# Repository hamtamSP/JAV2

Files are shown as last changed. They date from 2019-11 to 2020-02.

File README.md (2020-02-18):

# JAV²




## JAV² Tree Planting Vehicle

The JAV² Tree Planting Vehicle is inspired by the [#teamtrees](https://teamtrees.org/) initiative to plant 20 million trees before 2020. Hence, we created a Tracked Vehicle that can travel through uneven terrain to plant seeds so that they can turn into trees. The JAV² Tree Planting Vehicle is designed to be controlled through Wifi with a mobile device to enable it to plant the seeds in remote areas.

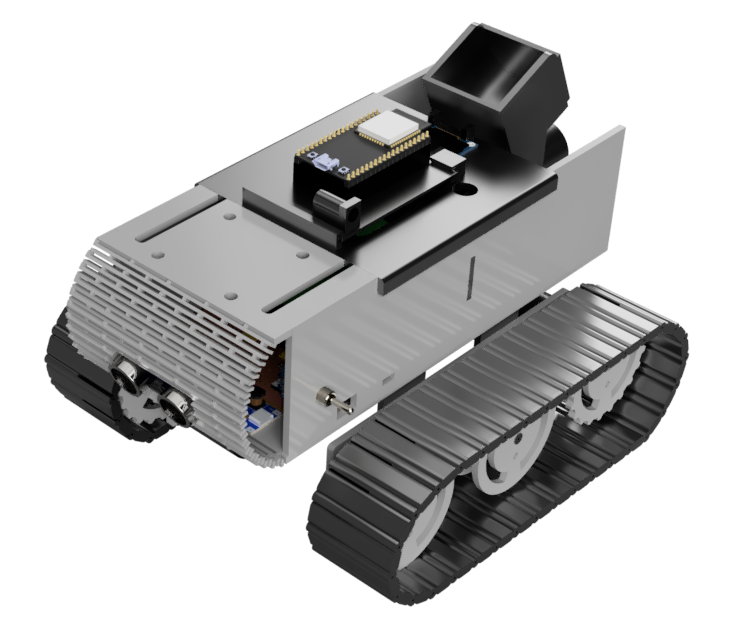
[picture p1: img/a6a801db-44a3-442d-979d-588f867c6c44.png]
JAV² Tree Planting Vehicle


## Table of Contents

- [Documentation](#documentation)
- [Features](#features)
- [Setup](#setup)
- [What You Will Need](#what-you-will-need)
- [Contributors](#contributors)

## Documentation

Documentations for JAV² can be found on GitHub at [https://github.com/hamtamSP/JAV2/blob/master/docs/Documentation.md](https://github.com/hamtamSP/JAV2/blob/master/docs/Documentation.md).

## Features

- Wireless Connectivity with Wifi.
- Auto Seed Dispensing
- Travel on Uneven Terrain

## What You Will Need

- JAV² Tree Planting Vehicle
- Seeds

## Setup

Fill Up the Hopper with Seeds.

Turn on the Tree Planting Vehicle by using the power switch located on the right side of the robot.

Connect to the Wireless AP on the ESP32 using the details on the OLED Screen.

Follow the instructions on the OLED Screen and Enter your wireless network credentials.

Connect to your wireless network and use the details on the OLED Screen to control the Tree Planting Vehicle.

## Contributors

Contributors to JAV² are listed here in alphabetical order. More detailed information about contributions can be found using the [git-commit history](https://github.com/hamtamSP/JAV2/commits/master) of the main branch.

- [@Darkmidget](https://github.com/Darkmidget) (Vincent Ho)
- [@DsouzaVirgil](https://github.com/DsouzaVirgil) (Virgil)
- [@hamtamSP](https://github.com/hamtamSP) (Arian Yap)
- [@JerenTong](https://github.com/JerenTong) (Jeren Tong)

### Blogs

Blogs can be found at:
- [Vincent](https://github.com/hamtamSP/JAV2/tree/master/Vincent_Adventure)
- [Virgil](https://github.com/hamtamSP/JAV2/tree/master/Virgil)
- [Arian](https://github.com/hamtamSP/JAV2/tree/master/Arian)
- [Jeren](https://github.com/hamtamSP/JAV2/tree/master/Jeren)

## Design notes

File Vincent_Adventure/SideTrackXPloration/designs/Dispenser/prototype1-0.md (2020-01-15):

# Dispenser 1.0 (G2 - Pen Design)

## Introduction
When I was in primary school, I like to make things that wasn't meant for the purpose of the product. One of them is a G2-Pen gun, where I disassemble the used pen and reconfigure it into a projectile shooter.

For this case, I will need to reconfigure the barrel size for the sapling to fit in the loading system. I will also redesign the firing system so that the firing force will be the sapling roots and not the leaves or stem. In order to ensure that the saplings is planted firmly to the ground, the saplings will have a tiny rock(Weight) in the roots system so that dispenser will have enough force to punch the saplings into the ground.

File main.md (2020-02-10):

# JAV²
[About Us]()

This site will be used as a group documentation when the project starts officially

This is the link to our contributions and research:

* [Hours Clocked](https://docs.google.com/spreadsheets/d/1DFZNll1I7CO4VDM-ied0fAtll_ErM5nZQO0H-ZwF12Y/edit#gid=0)

* [Group research and findings]()

* [Schematic](https://github.com/hamtamSP/JAV2/blob/master/Schematic-1.svg)

This will be our Individual Blogs
* [Vincent_Adventure](https://github.com/hamtamSP/JAV2/tree/master/Vincent_Adventure/Weekly)
*
## Problem Statements
* Tree  

## Idea Generation

* Tree planter

## What we want our Vehicle to do?
* What is the maximum velocity of the vehicle?
* How many horsepower does the vehicle need?
* How many horsepower does the vehicle need?
* What will be the energy consumption of the vehicle?
* How long does it take for the vehicle to come to stop?
* What happens if shock-absorbers don’t work?
* How to re-gain lost adhesion of the tire?
* What happens when the brake is suddenly applied during cornering?
* Understanding active vehicle safety

## Vehicle Drawing
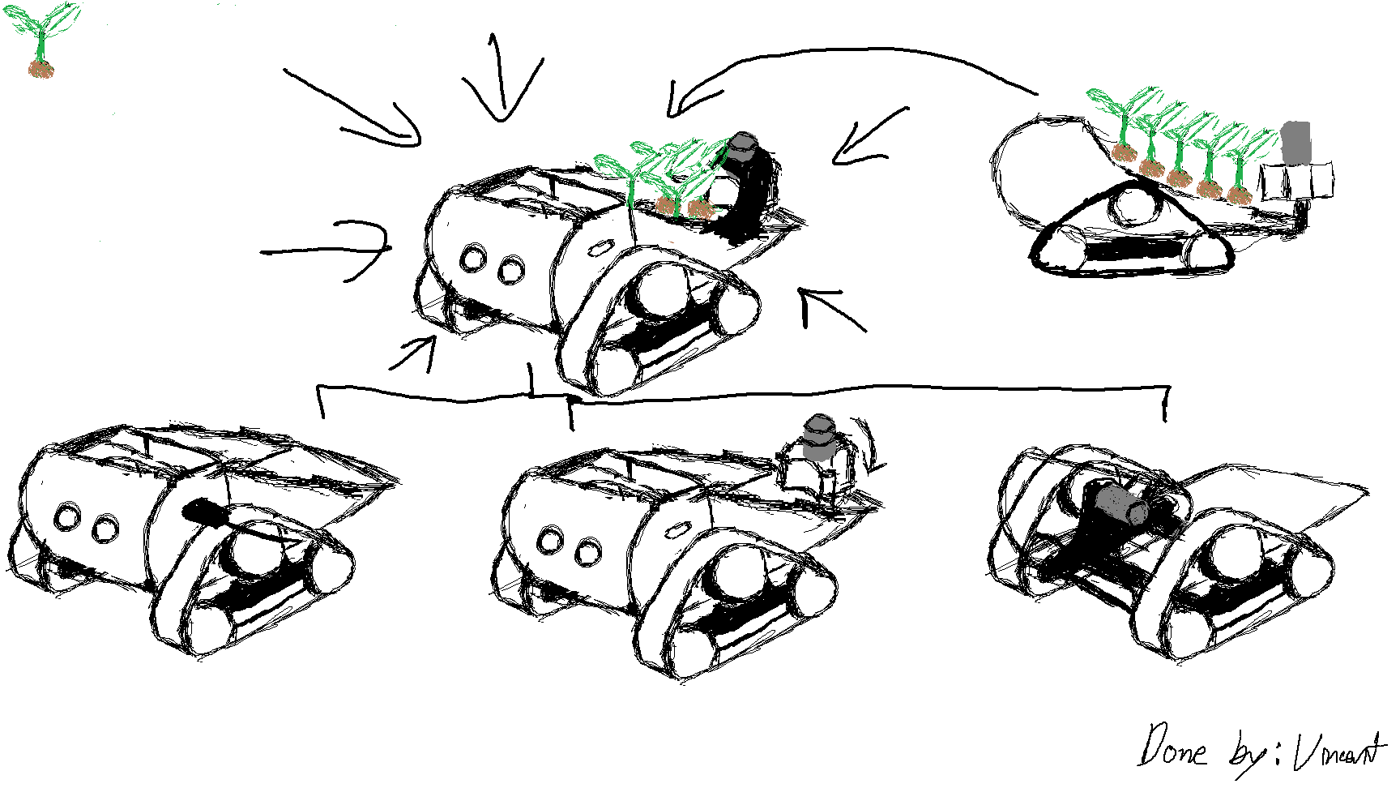
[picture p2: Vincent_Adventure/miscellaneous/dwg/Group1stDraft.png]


## Source Codes
* [Vehicle Run](https://github.com/hamtamSP/JAV2/blob/master/Vincent_Adventure/Blog/Source_code/vehicle%20run%20test%20(forward).py)
* [Vehicle Run with Web Server](https://github.com/hamtamSP/JAV2/blob/master/Vincent_Adventure/Blog/Source_code/WebControlEsp32.py)
* [OLED Library Code](https://github.com/hamtamSP/JAV2/blob/master/Virgil/ssd1306.py)
* [OLED Test Code](https://github.com/hamtamSP/JAV2/blob/master/Virgil/main.py)

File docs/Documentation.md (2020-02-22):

---
title: Documentation
subtitle: Documentation Page for JAV²
layout: page
show_sidebar: false
menubar: documentation
hide_footer: true
---


## Table of Contents

- [Getting Started](#getting-started)
- [Electrical Components](#electrical-components)
  - [Charging Circuit](#charging-circuit)
  - [Boost Ciruit](#boost-circuit)
  - [Battery Monitor](#battery-monitor)
- [Software](#software)
  - [Installation of Software](#installation-of-software)
  - [ESP32 Setup](esp32-setup)

## Getting Started

Below are the Components That are Used

- ESP32
- HC-SR04 Ultrasonic Sensor
- L298N H-Bridge
- 2 x TP4056 Charging Module
- 2 x 18650 Battery
- 2 x 1n4001 Diode
- DPDT Switch
- 2 x Boost Converter
- SG90 Servo
- 2 x Motors
- I2C OLED Display
- 2 x 3.9MΩ Resistors
- 2 x 2.2MΩ Resistors

To Program the ESP32, You will also need the following Software
- [Python](https://www.python.org/downloads/)
- [ESPTool](https://github.com/espressif/esptool)
- [Thonny](https://thonny.org/)
- [MicroPython](https://micropython.org/download)

## Electrical Components

### Charging Circuit

The TP4056 Charging Module is a Single Cell Charging Board. Hence, in order to charge two batteries at the same time, we will connect the 2 TP4056 Modules in Parallel. This allows us to take advantage of the protection features of the board as well as the capacity of the 2 batteries. The outputs of each TP4056 Module is then connected to a 1n4001 Diode to prevent reverse current due to differences in voltages from the 2 modules. The 2 Diodes are then connect to a DPDT Switch actings as a ON/OFF Switch for the Tree Planting Vehicle and the 2 connections are conbimed later. This can be shown in the schematics provided below.

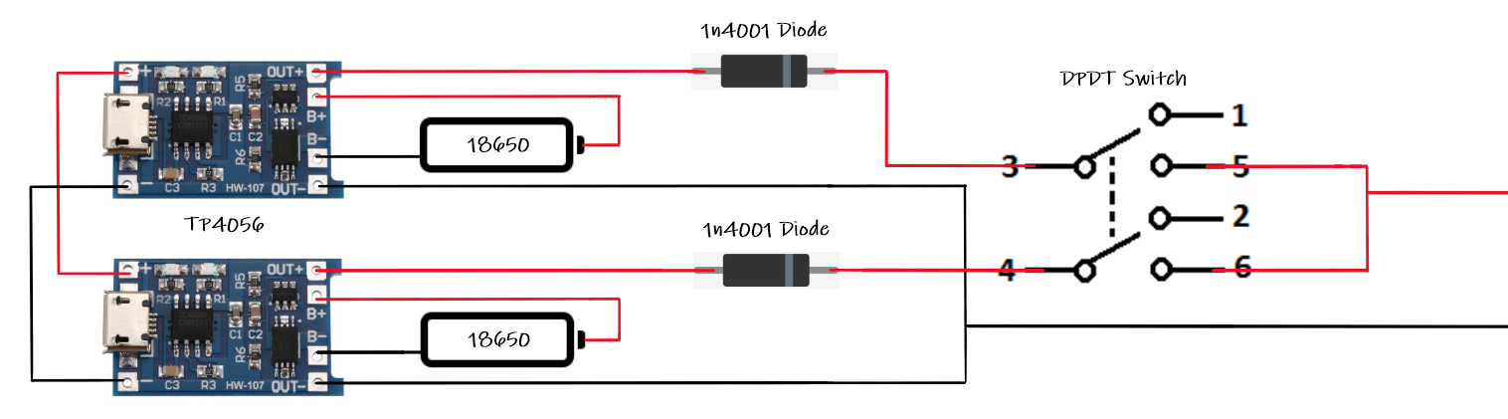
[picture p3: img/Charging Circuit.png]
Charging Circuit


### Boost Circuit

By connecting the output from the charging circuit to the input of the Boost Converter, we Can boost the voltage coming from the TP4056 to 11V for the L298N H-Bridge which is connected to the Output of the Boost Converter. The 5V Rail of the L298N can then be used to supply power to the ESP32 and the other pheripherials. This can be shown in the Schematics provided below.

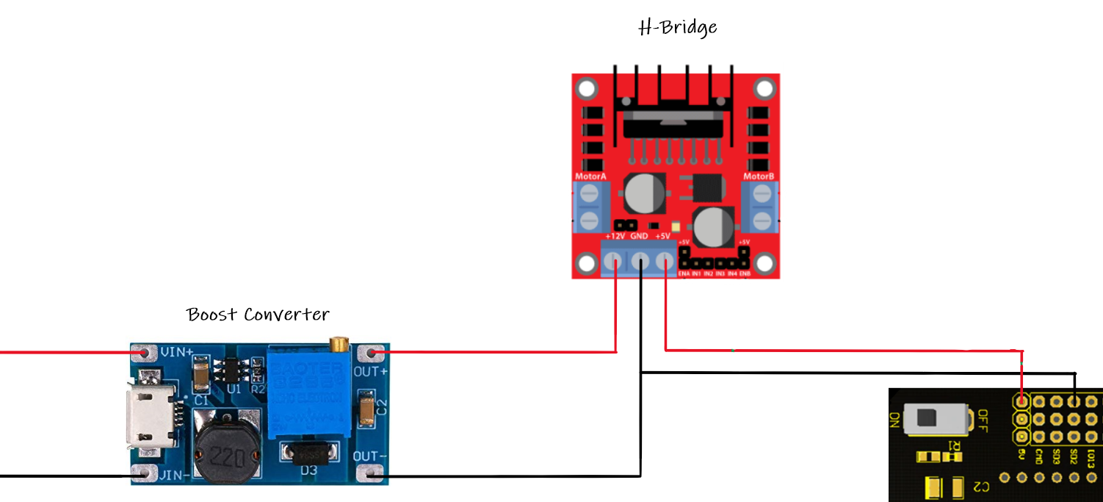
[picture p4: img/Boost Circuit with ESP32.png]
Boost Circuit with ESP32


However, the above circuit can only supply 500mA through the 5V rail due to the L298N H-Bridge. Hence, the L298N H-Bridge will only be used to provide power to the motors and a sperate circuit will be used to supply power to the ESP32 and the other pheripherials. This can be shown in the Schematics provided below.

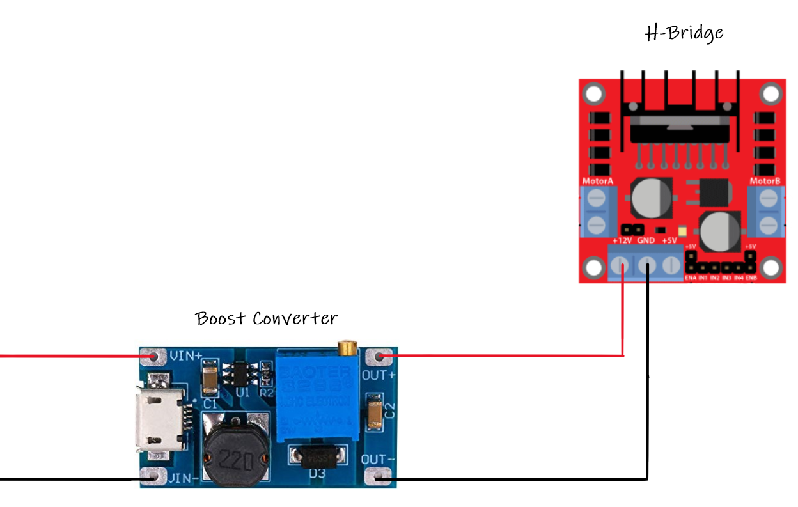
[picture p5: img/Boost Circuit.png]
Boost Circuit


### Battery Monitor

To relay the battery voltage to the ESP32 so that we will have the battery capacity, we would create a voltage divider as the ESP32 can only read up to 3.3V. Hence, we used 2 x 3.9MΩ Resistors and 2 x 2.2MΩ Resistors to create a voltage divider as shown in the schematics below.

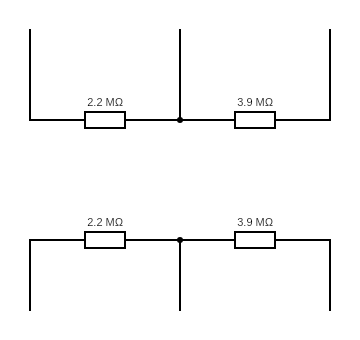
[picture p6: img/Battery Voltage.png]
Battery Monitor


## Software

### Installation of Software

To Download Python, Head to [https://www.python.org/downloads/](https://www.python.org/downloads/) and download the latest release of python. When prompted check "include PATH". After Python has been installed, Open command Prompt and enter:
``` pip install esptool ```

The install process will run and a message will show when the install is completed. (Message may differ depending on the version)

``` Successfully installed ecdsa-0.13.3 esptool-2.8 pyaes-1.6.1 pyserial-3.4 ```

Now you can also download and install the latest version of Thonny at [https://thonny.org/](https://thonny.org/).
You can also download the relevant version of MicroPython at [https://micropython.org/download](https://micropython.org/download)

### ESP32 Setup

The ESP32 is usually preinstalled with Lua and NodeMCU. But since we are using MicroPython, we will need to erase the flash. we can do this by using the following command on Command Prompt:

``` esptool.py --chip esp32 -p COM3 erase_flash ```

Note that `COM3` is the corresponding port connected to the ESP32. However if you recieved an error message like: `'esptool.py' is not recognized as an internal or external command, operable program or batch file.` use the folling command instead:

``` esptool.exe --chip esp32 -p COM3 erase_flash ```

To install MicroPython, Use the following command:

``` esptool.exe --chip esp32 -p COM3 write_flash -z 0x1000 esp32-idf3-20191106-v1.11-558-gd209f9ebe.bin ```

Note that `esp32-idf3-20191106-v1.11-558-gd209f9ebe.bin` is the MicroPython file where you just downloaded and `COM3` is the corresponding port connected to the ESP32.
Now you are all set to program the ESP32 with Thonny!

Next upload these files and save the files as the same name as stated in ESP32
![Workable files](https://github.com/hamtamSP/JAV2/tree/master/Vincent_Adventure/Blog/Source_code/workable)

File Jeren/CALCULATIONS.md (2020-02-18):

# Calculations
***
#### Mechanical Calculation
[Link to Mechanical Calculations Excel Sheet](https://github.com/hamtamSP/JAV2/blob/master/Jeren/TwVsT_accGraph.xlsx)
***
#### Maximum Incline
When vehicle is not moving:

Max. Incline = tan-1 (μs) , μs = surface coefficient

Dirt: Smooth = 1.43° , Sandy = 2.12°

Mud: Firm = 2.12° , Medium = 5.14° , Soft = 8.5°

When vehicle is moving:

θmax = 3.12°
***
#### Seed Dispensing Power Requirement
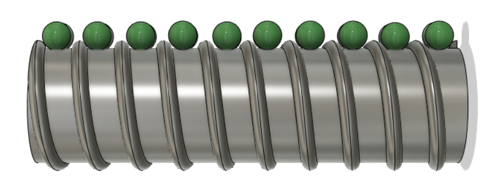
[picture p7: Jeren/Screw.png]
Screw


Mass of 1 green bean = 0.5g = 0.0005kg

Mass of 10 beans 	 = 0.005kg

Mass of the screw 	 = 6g = 0.006kg

Total Mass = 0.011kg

Angular Torque:
𝜏 = mrα

α = driver speed x π /       acceleration time x 30

=330π

𝜏 = (0.011)(0.0075)(330π)

= 0.0855Nm

Power = 𝜏 x 2π/30 = 0.018W

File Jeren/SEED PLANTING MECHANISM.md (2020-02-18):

# Seed Planting Mechanism
***
I was task to make a back-up plan in case the drilling mechanism did'nt work.
***
### Ideas
* Rather than putting the seed under the soil, maybe we could put soil over the seed
    * The problem with this is that the soil will give addition weight and maybe too much for the vehicle. It will also require another mechanism to dispense the soil.

Mr Tune said that putting the seed into the ground is very hard to do, recommends to just dispense the seed onto the ground, so i will be focusing on that.
***
### Prototype
Prototype 1

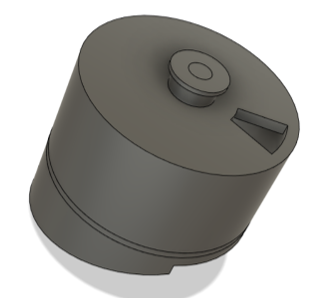
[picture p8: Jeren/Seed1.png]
Seed1
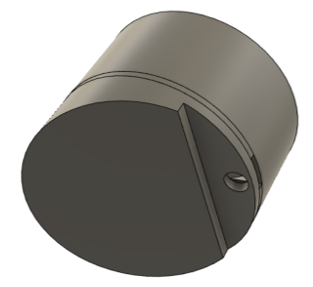
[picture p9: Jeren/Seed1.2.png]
Seed1


This design requires a belt attached to the top of the case and to a servo, Seed will be loaded into the hole at the top. The servo turns, causing the case to turn as well due to the belt. The angled stand will allow the the seeds to continuously fall.
The problem is that the seeds cannot stop falling.

Prototype 2

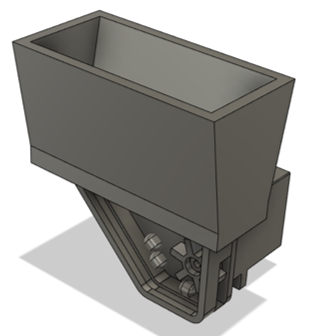
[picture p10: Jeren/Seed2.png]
Seed2


This prototype lets the seed fall into a pathway. The seeds should be pushed out by a gear. The gear is moved by the servo.
The problem the seed may get jammed by the gear and stop working, so it was discontinued. :(

Prototype 3

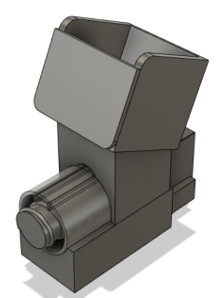
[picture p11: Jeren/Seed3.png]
Seed3


This prototype uses a screw to dispense the seeds. The seed will be loaded at the top and will drop in to the tube. The screw will push the seeds out by turning, moved by the servo. Vincent fixed some problems like seed jamming. He made the tube have a guiding path for the seed so that it won't get jammed (Though there may still be jamming sometimes). The stand allows the prototype stand onto the casing made by Vincent so that it can be assembled seperately and easily.

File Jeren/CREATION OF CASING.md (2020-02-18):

# Casing Creation
***
I was given the task to creating the casing of the tracked vehicle.
***
These designs were drawn by Vincent that i used as a reference.

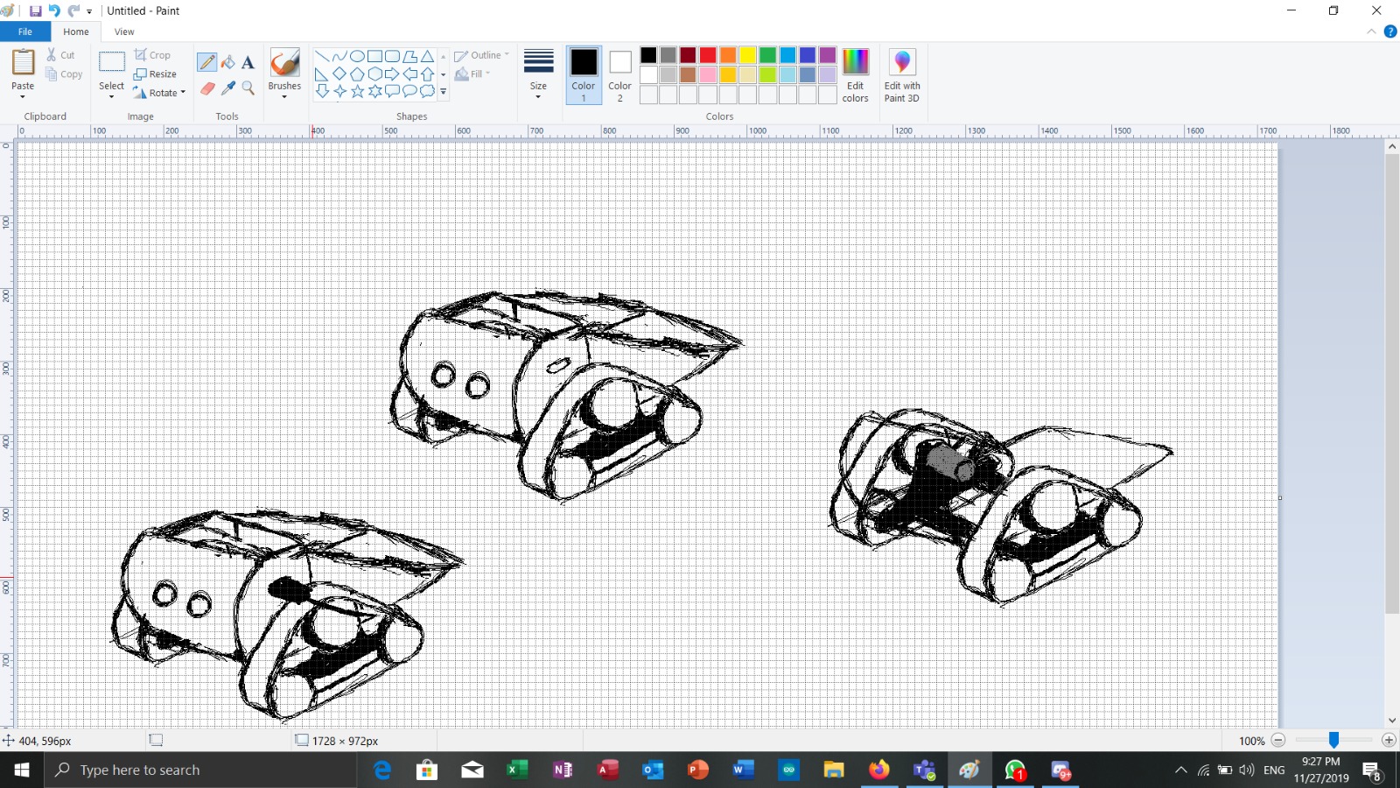
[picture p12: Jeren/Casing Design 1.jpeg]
Designpt1

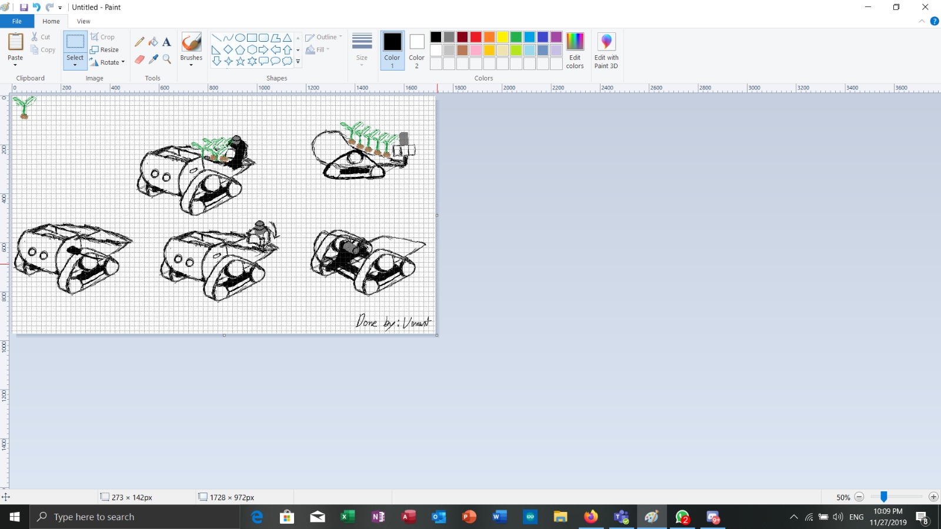
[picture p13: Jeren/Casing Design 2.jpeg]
Designpt2

***
I used inventor to create 3 versions of the casing
***
Version 1

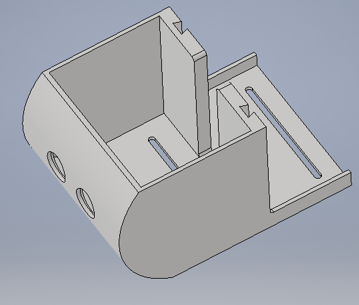
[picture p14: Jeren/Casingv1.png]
casingv1


This version is the basic casing where I follow the given design, There are holes at the front for mounting the esp32. The 2 slots on the base is for mounting onto the main chassis. There are 2 slots on the back wall. It is so that users can add any parts via an additional box. There is a gap on the back wall for the wires to run through.
***
Version 2

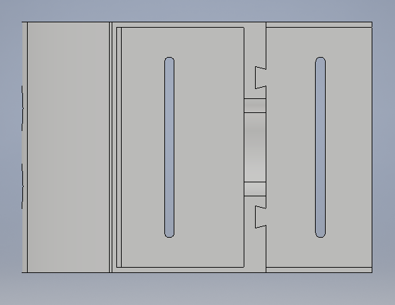
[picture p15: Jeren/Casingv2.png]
casingv2


This version has more accurate dimensions for almost all the holes and slots.

***
Version 3

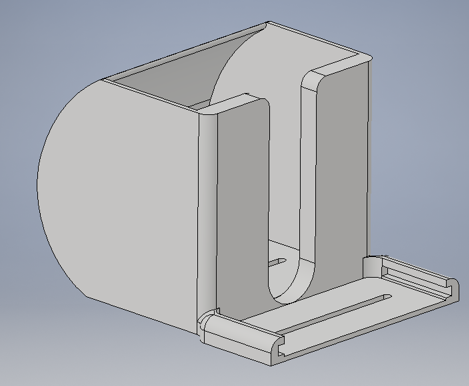
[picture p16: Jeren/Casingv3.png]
casingv3


This version has the mounting slots on the side as I thought is may be a better variant for the casing.
***
From here on, I used Fusion 360.
***
Version 4

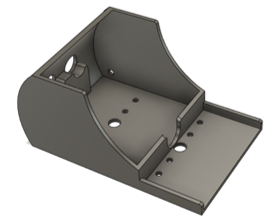
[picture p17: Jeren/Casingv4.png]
casingv3


I realised in the previous versions that due to the height of the walls, the assembly would be difficult as there is little space for tools and hands. So the main point of this is the lowered walls which would give easy assesibility. There is an extra stand for the ultrasonic sensor so that is is properly mounted. The slots to mount on to the main chassis were also changed to hole so that it would not move as much as before. There is a hole on the right wall for a toggle switch. The hole positions were a big problem for me.
***
Version 5
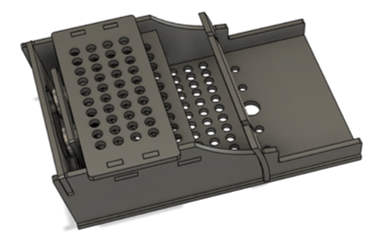
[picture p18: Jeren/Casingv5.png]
casingv3

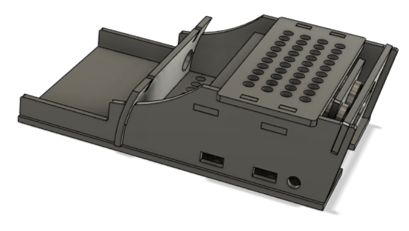
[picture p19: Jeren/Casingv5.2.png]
casingv3


For previous versions, i was thinking that it would be entirely produced through 3D-printing. But for this version, most of the parts would be produced through laser cutting. As seen in the image, there are a lot of holes. The holes are so that any components can be placed in the casing, rather than having the casing be used for this specific project. The back wall is curved. It works together with the slots on the wall to hold the extra compartment at the back. The wires will run through the holes of the back wall rather than a gap in the wall. The ultasonic sensor is made to face toward the floor, as requested by Vincent. The right side has three holes as seen on the image. The round hole is for the toggle switch. The 2 rectangular holes are for the usb, They are bigger than the required dimensions as Arian requested for space so that users can look for light.
For the assembly of this version, there are slots for fitting the workpieces. It kind of works like puzzle pieces.

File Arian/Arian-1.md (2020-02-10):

# Arian

Below contains the electrical schematic for the Track Vehicle

Schematic-1

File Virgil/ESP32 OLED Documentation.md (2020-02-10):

# ESP32 & OLED Display

The ESP32 allows the use of the 0.96 inch SSD1306 OLED to display
a certain output by controlling the pixels on the display. The
OLED display is controlled using I2C communication protocol. In
our case, the OLED will be used to display status of our tracked
vehicle.

## Connections

VCC: 3.3V<br/>
GND: GND<br/>
SCL: GPIO22<br/>
SDA: GPIO21

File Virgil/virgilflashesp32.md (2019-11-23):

# Introduction to ESP32

Author: Virgil D'souza

## Introduction

The ESP32 is a type of microcontroller
capable of operating in industrial
environments. It can operate at temperatures
ranging from -40&deg;C to 125&deg;C. It does
not require much power to function, making
it popular in applications for mobile
devices and IoT. The ESP32 is also capable of
WiFi and Bluetooth applications.

## Setting up the ESP32

The ESP32 is able to be programmed using Micropython provided
it is correctly configured. This section provides the essential
steps to wipe and flash the ESP32 with Micropython.

### Step 1: Installing python on Windows

To begin the flashing of the ESP32, python MUST be installed
onto the computer. Download from [here](python.org/downloads).
Ensure that you download the version that matches the operating
systems of the computer.

Once downloaded, start the install process. Follow the instructions
on the install wizard.

NOTE:
<br>Checkbox for creating a path should be checked.

### Step 2: Installing Binary File

Download the binary file for micropython from the
[Micropython downloads page](https://micropython.org/download#esp32).
Ensure that the file you download matches your operating system.
It is recommended that you choose the 'Generic' option.

Recommended: esp32-idf3-20191115-v1.11-580-g973f68780.bin

### Step 3: Installing ESPTool

Connect the ESP32 to the computer using micro-USB cable.

Run the command prompt and type in "pip install esptool".

The output on the command prompt should look like this:
C:\Users\dsouz>pip install esptool
Collecting esptool
  Downloading https://files.pythonhosted.org/packages/68/91/08c182f66fa3f12a96e754ae8ec7762abb2d778429834638f5746f81977a/esptool-2.8.tar.gz (84kB)
     |¦¦¦¦¦¦¦¦¦¦¦¦¦¦¦¦¦¦¦¦¦¦¦¦¦¦¦¦¦¦¦¦| 92kB 590kB/s
Collecting pyserial>=3.0 (from esptool)
  Downloading https://files.pythonhosted.org/packages/0d/e4/2a744dd9e3be04a0c0907414e2a01a7c88bb3915cbe3c8cc06e209f59c30/pyserial-3.4-py2.py3-none-any.whl (193kB)
     |¦¦¦¦¦¦¦¦¦¦¦¦¦¦¦¦¦¦¦¦¦¦¦¦¦¦¦¦¦¦¦¦| 194kB 1.3MB/s
Collecting pyaes (from esptool)
  Downloading https://files.pythonhosted.org/packages/44/66/2c17bae31c906613795711fc78045c285048168919ace2220daa372c7d72/pyaes-1.6.1.tar.gz
Collecting ecdsa (from esptool)
  Downloading https://files.pythonhosted.org/packages/a2/25/3bb32da623b39a27a07d194cd58e4540224421d924661de2e694304ae4fa/ecdsa-0.14.1-py2.py3-none-any.whl (79kB)
     |¦¦¦¦¦¦¦¦¦¦¦¦¦¦¦¦¦¦¦¦¦¦¦¦¦¦¦¦¦¦¦¦| 81kB 880kB/s
Collecting six (from ecdsa->esptool)
  Downloading https://files.pythonhosted.org/packages/65/26/32b8464df2a97e6dd1b656ed26b2c194606c16fe163c695a992b36c11cdf/six-1.13.0-py2.py3-none-any.whl
Installing collected packages: pyserial, pyaes, six, ecdsa, esptool
  Running setup.py install for pyaes ... done
  Running setup.py install for esptool ... done
Successfully installed ecdsa-0.14.1 esptool-2.8 pyaes-1.6.1 pyserial-3.4 six-1.13.0
WARNING: You are using pip version 19.2.3, however version 19.3.1 is available.
You should consider upgrading via the 'python -m pip install --upgrade pip' command.

### Step 4: Flashing micropython to ESP32

Next, type in "esptool.py --port /dev/ttyUSB0 erase_flash"

NOTE: <br>
Replace "/dev/ttyUSB0" with your computer's communication port (COMX).

The output should look like this:

C:\Users\dsouz>esptool.py --chip esp32 --port COM6 erase_flash
esptool.py v2.8
Serial port COM6
Connecting.....
Chip is ESP32D0WDQ5 (revision 1)
Features: WiFi, BT, Dual Core, 240MHz, VRef calibration in efuse, Coding Scheme None
Crystal is 40MHz
MAC: 4c:11:ae:71:14:08
Uploading stub...
Running stub...
Stub running...
Erasing flash (this may take a while)...
Chip erase completed successfully in 9.6s
Hard resetting via RTS pin...

Next, type in "esptool.py --chip esp32 --port /dev/ttyUSB0 write_flash -z 0x1000 esp32-20180511-v1.9.4.bin",
again replacing "/dev/ttyUSB0" with the COM port on your computer. To avoid
any typo, drag the file into the command prompt. The file name will
appear.

The output should look something like this:

C:\Users\dsouz>esptool.py --chip esp32 --port COM6 --baud 460800 write_flash -z 0x1000 C:\Users\dsouz\Downloads\esp32-idf3-20191113-v1.11-576-gd667bc642.bin
esptool.py v2.8
Serial port COM6
Connecting.....
Chip is ESP32D0WDQ5 (revision 1)
Features: WiFi, BT, Dual Core, 240MHz, VRef calibration in efuse, Coding Scheme None
Crystal is 40MHz
MAC: 4c:11:ae:71:14:08
Uploading stub...
Running stub...
Stub running...
Changing baud rate to 460800
Changed.
Configuring flash size...
Auto-detected Flash size: 4MB
Compressed 1240160 bytes to 783158...
Wrote 1240160 bytes (783158 compressed) at 0x00001000 in 18.9 seconds (effective 524.5 kbit/s)...
Hash of data verified.

Leaving...
Hard resetting via RTS pin...

### Step 5: Launching Thonny

Launch Thonny, go to Run > select interpreter and select Micropython(generic).
Select the COM port according to your computer.

Once the options are selected, you should be able to see a
message that the ESP32 has been detected.

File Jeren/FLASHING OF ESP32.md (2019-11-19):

# Flashing of esp32
---
References:

https://learn.sparkfun.com/tutorials/how-to-load-micropython-on-a-microcontroller-board/esp32-thing
***
What you need:
* Python 2.7 or Python 3.4 or newer
* esp32
---
## Steps:
#### 1) Install esptool
open command prompt and input this command
`pip install esptool`

### 2) Erase everything on the chip's flash memory
input this command:
`esptool.exe --chip esp32 -p <USB to serial port> erase_flash`
<USB to serial port> is got from device manager

### 3) Install firmware from https://micropython.org/download#esp32
There are 2 types of firmware for us to choose from
* Firmware built with ESP-IDF v3.x, with support for LAN and PPP but no bluetooth
* Firmware built with ESP-IDF v4.x, with support for bluetooth but no LAN or PPP

Recommended firmware: esp32-idf3-20191106-v1.11-558-gd209f9ebe.bin
This recommended firmware comes from the first catergory.
   
### 4) Flash the firmware with this command:
`esptool.exe --chip esp32 -p <USB-to-Serial Port> write_flash -z 0x1000 <path to .bin>`
<path to .bin> is the path to the location of the .bin file

##### With these steps, the Micropython firmware is now installed onto the esp32.
***
## Problems faced:
The main problem I faced was that I did not install python correctly and was struggling to get the code to work as there was a prompt that there was a syntax error. This happened because I did not check 'Add Python 3.8 to PATH'.
Another problem was that the reference website showed to use the command `esptool.py`, it did not work for me, which was very troubling. But this was solved as we noticed that the command was 'downloaded' as `esptool.exe`.

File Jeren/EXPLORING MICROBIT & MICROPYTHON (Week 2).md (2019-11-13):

# EXPLORING MICROBIT & MICROPYTHON
##### Week 2
***
## Introduction
As seen form the title, we will be looking into microbit.
***
## What is a microbit?
A microbit is "a pocket-sized computer 70 times smaller and 18 times faster than the original BBC Micro computers used in schools. It has 25 red LED lights that can flash messages and be used to create games.", a short description of the microbit from the [BBC microbit website](https://support.microbit.org/support/solutions/articles/19000013983-what-is-a-micro-bit-).
Microbits can be used in gaming consoles and communication devices.
***
## Coding
##### What I used for these exercises:
* Microbit
* Thonny app (version 3.2.1) , to code the microbit using micropython
##### Code 1
The first execise we tried in class was to make a heart appear on the microbit.
This is the code I wrote:
```
from microbit import *

display.show(Image.HEART)
```
This will display a heart on the lights of the microbit.

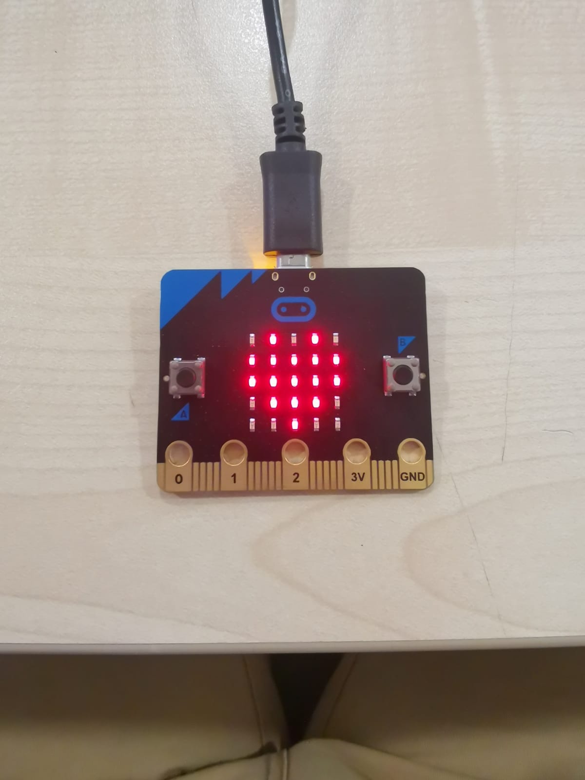
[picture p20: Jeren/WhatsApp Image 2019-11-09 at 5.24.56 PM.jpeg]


What i learnt for this exercise:
* Writing the first line, `from microbit import *` is very important as it allows you to get saved data from the microbit, for example, the heart image.
* When writing the second line `display.show(Image.HEART)`, the word 'HEART' has to be capitalised, otherwise the word will not be recognised

##### Code 2
This second exercise was to learn about displaying messages.
This is the code i wrote:
```
from microbit import *

while True:
    display.scroll("Hello World")
```
The outcome was that the message in the quotes will scroll across the microbit LEDs, as seen below.



What I learnt from this exercise:
* Learnt the scroll function
* Using `while True:` gives you a loop that makes the message countiuously scoll across the LED

##### Code 3
The third exercise is to learn how to create our own personalized images with the LEDs. We were first tasked to design a boat.
This is the code i wrote:
```
from microbit import *

while True:
    boat = Image("00500:"
                  "00550:"
                  "00500:"
                  "55555:"
                  "05550")
    display.show(boat)
```
The numbers in the quotations represents the LEDs on the microbit in a 5x5, where '0' is off and any nuber from 1-9 is on, where 1 is the dimmest and 9 is the brightest. When the code is uploaded, the microbit will display a the image you create, a boat in this context.

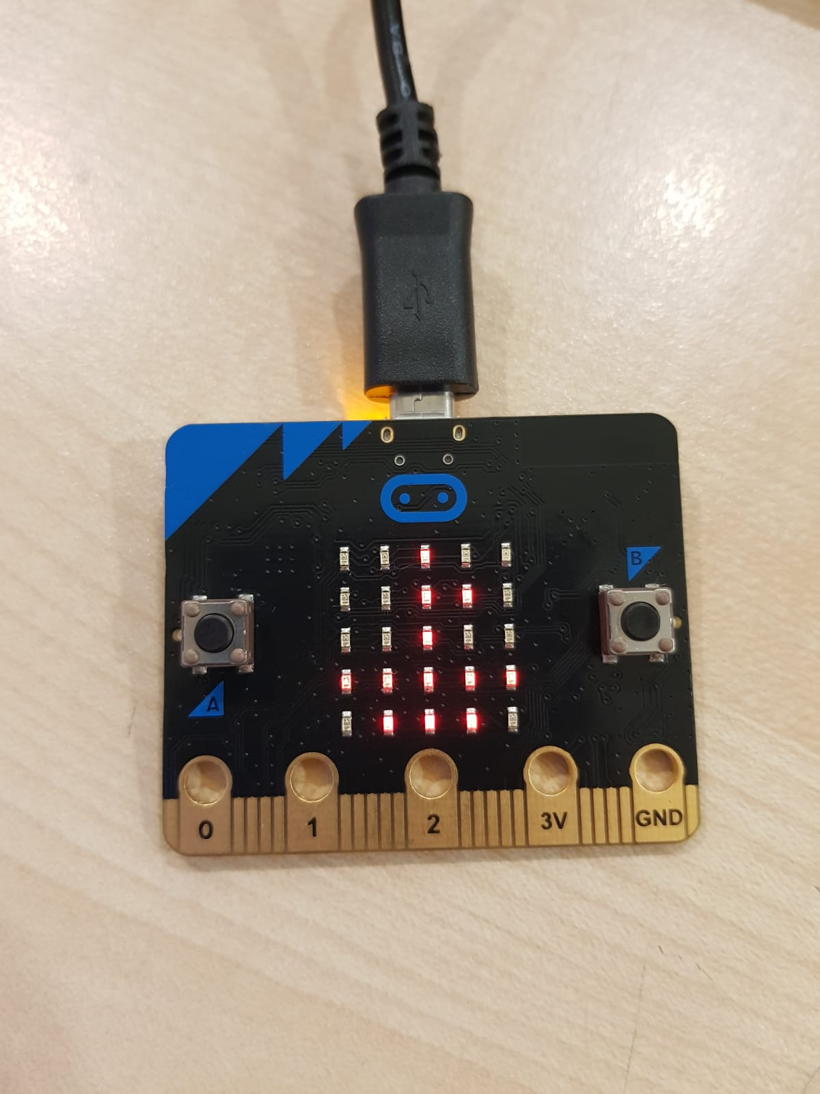
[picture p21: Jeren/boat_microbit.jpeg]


The second part of this exercise was to make the boat look animated, floating up and down.
This is the code I wrote:
```
from microbit import *

while True:
    boat1 = Image("00500:"
                  "00550:"
                  "00500:"
                  "55555:"
                  "05550")
    display.show(boat1)
    sleep(1000)
    
    boat2 = Image("00000:"
                  "00500:"
                  "00550:"
                  "00500:"
                  "55555")
    display.show(boat2)
    sleep(1000)
```

What I learnt from this exercise:
* By using `sleep()`, we are able to make a delay so that the image on the LED does not change immediately.

##### Code 4
The forth code was to learn how to programme the 2 buttons on the microbit to change the LEDs.
Our task:
* Happy face shown when no buttons are pressed
* Sad face shown when Button A pressed
* Angry face shown when button B pressed

This is my code:
```
from microbit import *

while True:
    if button_a.is_pressed():
        display.show(Image.SAD)
    elif button_b.is_pressed():
        display.show(Image.ANGRY)
    else: display.show(Image.HAPPY)
```
This is how it turned out:



What i learnt from this exercise:
* The image you want to display when no buttons are pressed has to be at the back, because of priority, otherwise the microbit will flash both images at the same time
* Since i used C++ first, I was used to its functions, so when i wrote `else if`, it did not work for me and was confused. When I googled, I found out that `elif` had to be used
* For the `else:` function, you have to make sure to include the ':', otherwise it will not be recognised

Next, we had to make it so that when both buttons were pressed at the same time, something else would be displayed.
This is my code:
```
from microbit import *

while True:
    if button_a.is_pressed() and button_b.is_pressed():
        display.show(Image.HEART)
    elif button_a.is_pressed():
        display.show(Image.SAD)
    elif button_b.is_pressed():
        display.show(Image.ANGRY)
    else: display.show(Image.HAPPY)
```
What I learnt from this exercise:
* For the priority, the line for when both buttons were pressed was put on to so that it would prioritize that line first, otherwise it will not appear at all

##### Code 5
For this exercise, we were tasked to make the microbit display different images when different actions were done to the microbit. This exercise makes use of the microbit's motion sensors (accelerometer & compass).
These are the gestures (and codes) the microbit is able to recognise:
* up
* down
* left
* right
* face up
* face down
* freefall
* 3g
* 6g
* 8g
* shake

This is the code I wrote:
```
from microbit import *

while True:
    gesture = accelerometer.current_gesture()
    if gesture == "face up":
        display.show(Image.HAPPY)
    elif gesture == "face down":
        display.show(Image.ANGRY)
    elif gesture == "left":
        display.show(Image.HEART)
    else: display.show(Image.SURPRISED)
```
The results basically show a/an:
* Happy fave when the microbit(LED side) is faced up
* Angry face when the microbit is faced down
* Heart when the microbit faces left
* Surprised face when the microbit does not do any of those gestures

##### Code 6
This exercise teaches us how to make a randomizer in the microbit with micropython.

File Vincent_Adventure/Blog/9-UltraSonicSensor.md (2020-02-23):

# Ultra Sonic Sensor

### Introduction
In my seed planting vehicle, I am going to put an ultra sonic sensor at the front of the vehicle so that I am able to know if there is a potential danger in the path that the vehicle is about to go. The ultra sonic sensor will be places that a -20 degree parallel from the ground facing downwards. It is the stimulate if the vehicle is near a cliff or of there obstacle blocking its path

### Control of Ultra Sonic Sensor

I refer to this documentation:
(HC-SR04 Sensor driver in micropython)[https://github.com/rsc1975/micropython-hcsr04]

### How to use:

1. Download hcsr04.py from (here)[https://github.com/rsc1975/micropython-hcsr04/blob/master/hcsr04.py]
2. Save the file inside ESP32 and use the command stated in (here)[https://github.com/rsc1975/micropython-hcsr04] to use

3. Done

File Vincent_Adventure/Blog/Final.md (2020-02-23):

# Final Combined Code
### Introduction
After going through all the steps, we are going to combine all the things we have learnt into the vehicle

### Steps
1. Download/Ensure that all the files in (here)[https://github.com/hamtamSP/JAV2/tree/master/Vincent_Adventure/Blog/Source_code/workable] are inside ESP32.

2. Assemble and connect the circuit accordingly

3. Run the entire setup.
### This is how it should work

Youtube: (ESP 32(micropython) Basic Web Control)[https://youtu.be/rKEyfn3Tat4]

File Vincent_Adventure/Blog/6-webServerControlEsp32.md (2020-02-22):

# ESP32 Web Control
## Reference
I referred to this documentation on RandomNerdTutorial:   
[MicroPython: ESP32/ESP8266 Access Point (AP)](https://randomnerdtutorials.com/micropython-esp32-esp8266-access-point-ap/)

I made some minor modification on top of the code referenced. Since I am going to use a website to control the Esp32, I added in lines of code where I change changed the address of the Website and how I want control it.

The flow will be something like this.
![]()

This is a sample code I have written:
      import usocket as socket
      except:
      import socket

      import network

      import esp
      esp.osdebug(None)

      import gc
      gc.collect()
      # =====================================================================
      import time
      import machine
      # =====================================================================
      ssid = 'Mapper'
      password = 'JokesOnYou'

      ap = network.WLAN(network.AP_IF)
      ap.active(True)
      ap.ifconfig(('192.168.16.4','255.255.255.0', '192.168.12.1', '8.8.8.8'))
      ap.config(essid=ssid, password=password, authmode = 3)

      while ap.active() == False:
      pass
      # =====================================================================
      print('Setup Successful')
      time.sleep(1)
      print(str(ap.ifconfig()))
      line = ['Setup Successful','Listening at...',str(ap.ifconfig()),'']
      time.sleep(0.1)

      def web_page(line):

      STATUS = line[0]
      STATUS2 = line[1]
      STATUS3 = line[2]

      html ="""<html>
      <head>
        <title>ESP Web Server</title>
        <meta name="viewport" content="width=device-width, initial-scale=1">
        <meta http-equiv="refresh" content="1; url=waiting">
        <link rel="icon" href="data:,">
        <style>

          html {
            font-family: Helvetica;
            display: inline-block;
            margin: 0px auto;
            text-align: center;
            background-color: Black;
            color: Green;
            font-size: 20;
          }

          h1 {
            color: White;
            padding: vh;
          }
          h2 {
            color: Green;
            padding: vh;
          }

          p {
            font-size: 1.5rem;
            margin:5px;
            color: White;
          }

          .button {
            display: inline-block;
            background-color: red;
            border: none;
            border-radius: 20px;
            color: White;
            padding: 10px 20px;
            text-decoration: none;
            font-size: 30px;
            margin: 1px;
            cursor: pointer;
          }

          .button2 {
            background-color: #e7bd3b;
            display: inline-block;
            border: none;
            border-radius: 20px;
            color: White;
            padding: 10px 20px;
            text-decoration: none;
            font-size: 30px;
            margin: 1px;
            cursor: pointer;
          }
          .button3{
            background-color: #e7bd3b;
            display: inline-block;
            border: none;
            border-radius: 20px;
            color: Green;
            padding: 10px 20px;
            text-decoration: none;
            font-size: 30px;
            margin: 1px;
            cursor: pointer;
          }
          section {
            float: left;
            width: 50%;
          }
          aside {
            float: right;
            width: 50%;
          }
          .footer {
            position: fixed;
            left: 0;
            bottom: 0;
            width: 100%;
            color: white;
            text-align: center;
          }
        </style>
      </head>
      <body>

          <h1>ESP Web Control</h1>
          <h2>""" + STATUS + """</h2>
          <h2>""" + STATUS2 + """</h2>
          <h2>""" + STATUS3 + """</h2>
        <section>
          <h1>Control</h1>
          <p><a href="/?forward"><button class="button button2">^</button></a></p>
          <p><a href="/?left"><button class="button button2"><</button></a><a href="/?stop"><button class="button button"><span>&#9888;</span></button></a><a href="/?right"><button class="button button2">></button></a></p>
          <p><a href="/?back"><button class="button button2">v</button></a></p>
        </section>
        <aside>
          <h1>Dispense</h1>
          <p><a href="/?deploy"><button class="button button3"><strong>DEPLOY!!</strong></button></a></p>
          <p><a href="/?reload"><button class="button button3"><strong>Reload</strong></button></a></p>
          <a href="/?Auto"><button class="button button3"><strong>Auto Plant</strong></button></a>
          <h1></h1>
        </aside>

      </body>

      </html>"""

      return html

      s = socket.socket(socket.AF_INET, socket.SOCK_STREAM)
      s.bind(('', 80))
      s.listen(5)

      line = ['','','','']

      while True:
      conn, addr = s.accept()
      print('Got a connection from %s' % str(addr))
      request = conn.recv(1024)
      request = str(request)
      print('Content = %s' % request)
      # =====================================================================

      forward = request.find('/?forward')
      back = request.find('/?back')
      left = request.find('/?left')
      right = request.find('/?right')
      stop = request.find('/?stop')

      if left == 6:
          print ("Left")
          line[0] = 'Left'
          mc.rotationLeft()
          time.sleep(0.1)
          print ("Stop")
          mc.stop()
      if right == 6:
          print ("Right")
          line[0] = 'Right'
          mc.rotationRight()
          time.sleep(0.1)
          print ("Stop")
          mc.stop()
      if stop == 6:
          print ("Stop")
          line[0] = 'Stop'
          mc.stop()
      if forward == 6:
          print ("Forward")
          line[0] = 'Forward'
          mc.fwd()
      if back == 6:
          print ("Reverse")
          line[0] = 'Reverse'
          mc.back()
      if dispense == 6:
          print("Dispensing")
          line[0] = 'Dispensing'
          mc.stop()
          time.sleep(1)
          o.display_(line)
          dispense_()
          line[0] = 'Dispensed'
      # =====================================================================
      response = web_page(line)
      conn.send(response)
      conn.close()

I will use Python's list to store information and update the webpage.

Refer the [MicroPython: ESP32/ESP8266 Access Point (AP)](https://randomnerdtutorials.com/micropython-esp32-esp8266-access-point-ap/) for the Understanding of code

I changed the layout of the html page which will look something like this, where the status will be updated with information from the robot.
!()[https://github.com/hamtamSP/JAV2/blob/master/Vincent_Adventure/Blog/pic/website/ESP32%20webcontrol/html_layout.png]

This line under the html section will refresh the page every 1 second and update the Url with 192.168.16.4/waiting:   

        <meta http-equiv="refresh" content="1; url=waiting">

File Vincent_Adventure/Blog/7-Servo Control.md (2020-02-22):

# Servo control

### Introduction
there are existing codes written in Micropython to control servo motors. However, they did not work so I will be controlling the servo motor from scratch.

### How the Servo works

!(How the Servo works)[https://github.com/hamtamSP/JAV2/blob/master/Vincent_Adventure/Blog/pic/website/Servo%20Control/Servo%20Control%20works.png]

Servo Motor are controlled using pulse where we have adjust the pulse in such that the servomotor will rotation in the direction that we want. I will being using the standard pwm code to control a continuous servo motor the       

      frequency = 1000 = min_pulse (Anti-Clockwise)
      frequency = 500 = max_pulse (Clockwise)

In micropython, to control pwm, we need to state the frequency and the duty for the pwm to work correctly. For more info, please refer to (this Documentation)[https://docs.micropython.org/en/latest/esp8266/tutorial/pwm.html].

### My code to control the my servoMotor
I am using a(continuous servo motor(MG90S) for my project to rotate the worm gear that my team mate designed for our seed dispenser. The servo will required to rotate anti-clockwise to dispense the seeds out.

My servo will be connect to:

        3.3v     red
        Ground   Black
        Pin 5    Orange
My code

        import machine
        import time
        while True:
        servo = machine.PWM(machine.Pin(5), freq=1000)
        servo.duty(200)
        time.sleep(0.55*7)

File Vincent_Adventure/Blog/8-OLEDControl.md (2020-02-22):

# OLed Display using esp32 (micropython)

### Introduction
My vehicle will be disconnected from my computer and it will run independently. There is no way, I can see what is going on with my esp32. I need to know the status that the vehicle is in and what address is it connected to. So I will be including an OLED display that will print out the status. I will be presetting the print outs in the esp32 and store the information as string into a list.

There is an existing library that is written in the Micropython processing language.

RandomNerds Tutorial:

(MicroPython: OLED Display with ESP32 and ESP8266)[https://randomnerdtutorials.com/micropython-oled-display-esp32-esp8266/]

I followed the example and realized that I have the clear the OLED display screen everytime I want to write in the same line. I created another python file just for the OLED Control.

### Step 1
Save SSD1306 OLED Library into the ESP32 and save as      

Ssd1306.py

      #MicroPython SSD1306 OLED driver, I2C and SPI interfaces created by Adafruit

      import time
      import framebuf

      # register definitions
      SET_CONTRAST        = const(0x81)
      SET_ENTIRE_ON       = const(0xa4)
      SET_NORM_INV        = const(0xa6)
      SET_DISP            = const(0xae)
      SET_MEM_ADDR        = const(0x20)
      SET_COL_ADDR        = const(0x21)
      SET_PAGE_ADDR       = const(0x22)
      SET_DISP_START_LINE = const(0x40)
      SET_SEG_REMAP       = const(0xa0)
      SET_MUX_RATIO       = const(0xa8)
      SET_COM_OUT_DIR     = const(0xc0)
      SET_DISP_OFFSET     = const(0xd3)
      SET_COM_PIN_CFG     = const(0xda)
      SET_DISP_CLK_DIV    = const(0xd5)
      SET_PRECHARGE       = const(0xd9)
      SET_VCOM_DESEL      = const(0xdb)
      SET_CHARGE_PUMP     = const(0x8d)

      class SSD1306:
      def __init__(self, width, height, external_vcc):
      self.width = width
      self.height = height
      self.external_vcc = external_vcc
      self.pages = self.height // 8
      # Note the subclass must initialize self.framebuf to a framebuffer.
      # This is necessary because the underlying data buffer is different
      # between I2C and SPI implementations (I2C needs an extra byte).
      self.poweron()
      self.init_display()

      def init_display(self):
      for cmd in (
          SET_DISP | 0x00, # off
          # address setting
          SET_MEM_ADDR, 0x00, # horizontal
          # resolution and layout
          SET_DISP_START_LINE | 0x00,
          SET_SEG_REMAP | 0x01, # column addr 127 mapped to SEG0
          SET_MUX_RATIO, self.height - 1,
          SET_COM_OUT_DIR | 0x08, # scan from COM[N] to COM0
          SET_DISP_OFFSET, 0x00,
          SET_COM_PIN_CFG, 0x02 if self.height == 32 else 0x12,
          # timing and driving scheme
          SET_DISP_CLK_DIV, 0x80,
          SET_PRECHARGE, 0x22 if self.external_vcc else 0xf1,
          SET_VCOM_DESEL, 0x30, # 0.83*Vcc
          # display
          SET_CONTRAST, 0xff, # maximum
          SET_ENTIRE_ON, # output follows RAM contents
          SET_NORM_INV, # not inverted
          # charge pump
          SET_CHARGE_PUMP, 0x10 if self.external_vcc else 0x14,
          SET_DISP | 0x01): # on
          self.write_cmd(cmd)
      self.fill(0)
      self.show()

      def poweroff(self):
      self.write_cmd(SET_DISP | 0x00)

      def contrast(self, contrast):
      self.write_cmd(SET_CONTRAST)
      self.write_cmd(contrast)

      def invert(self, invert):
      self.write_cmd(SET_NORM_INV | (invert & 1))

      def show(self):
      x0 = 0
      x1 = self.width - 1
      if self.width == 64:
          # displays with width of 64 pixels are shifted by 32
          x0 += 32
          x1 += 32
      self.write_cmd(SET_COL_ADDR)
      self.write_cmd(x0)
      self.write_cmd(x1)
      self.write_cmd(SET_PAGE_ADDR)
      self.write_cmd(0)
      self.write_cmd(self.pages - 1)
      self.write_framebuf()

      def fill(self, col):
      self.framebuf.fill(col)

      def pixel(self, x, y, col):
      self.framebuf.pixel(x, y, col)

      def scroll(self, dx, dy):
      self.framebuf.scroll(dx, dy)

      def text(self, string, x, y, col=1):
      self.framebuf.text(string, x, y, col)

      class SSD1306_I2C(SSD1306):
      def __init__(self, width, height, i2c, addr=0x3c, external_vcc=False):
      self.i2c = i2c
      self.addr = addr
      self.temp = bytearray(2)
      # Add an extra byte to the data buffer to hold an I2C data/command byte
      # to use hardware-compatible I2C transactions.  A memoryview of the
      # buffer is used to mask this byte from the framebuffer operations
      # (without a major memory hit as memoryview doesn't copy to a separate
      # buffer).
      self.buffer = bytearray(((height // 8) * width) + 1)
      self.buffer[0] = 0x40  # Set first byte of data buffer to Co=0, D/C=1
      self.framebuf = framebuf.FrameBuffer1(memoryview(self.buffer)[1:], width, height)
      super().__init__(width, height, external_vcc)

      def write_cmd(self, cmd):
      self.temp[0] = 0x80 # Co=1, D/C#=0
      self.temp[1] = cmd
      self.i2c.writeto(self.addr, self.temp)

      def write_framebuf(self):
      # Blast out the frame buffer using a single I2C transaction to support
      # hardware I2C interfaces.
      self.i2c.writeto(self.addr, self.buffer)

      def poweron(self):
      pass

      class SSD1306_SPI(SSD1306):
      def __init__(self, width, height, spi, dc, res, cs, external_vcc=False):
      self.rate = 10 * 1024 * 1024
      dc.init(dc.OUT, value=0)
      res.init(res.OUT, value=0)
      cs.init(cs.OUT, value=1)
      self.spi = spi
      self.dc = dc
      self.res = res
      self.cs = cs
      self.buffer = bytearray((height // 8) * width)
      self.framebuf = framebuf.FrameBuffer1(self.buffer, width, height)
      super().__init__(width, height, external_vcc)

      def write_cmd(self, cmd):
      self.spi.init(baudrate=self.rate, polarity=0, phase=0)
      self.cs.high()
      self.dc.low()
      self.cs.low()
      self.spi.write(bytearray([cmd]))
      self.cs.high()

      def write_framebuf(self):
      self.spi.init(baudrate=self.rate, polarity=0, phase=0)
      self.cs.high()
      self.dc.high()
      self.cs.low()
      self.spi.write(self.buffer)
      self.cs.high()

      def poweron(self):
      self.res.high()
      time.sleep_ms(1)
      self.res.low()
      time.sleep_ms(10)
      self.res.high()

### Step 2
Open a new file, copy the file below and save in ESP32 as

oLedControl.py

      from machine import Pin, I2C
      import ssd1306
      from time import sleep

      i2c = I2C(-1, scl=Pin(22), sda=Pin(21))

      oled_width = 128
      oled_height = 64
      oled = ssd1306.SSD1306_I2C(oled_width, oled_height, i2c)
      def reset():
      oled.fill(0)

      def display_(line):
      reset()
      #         text     null,line
      oled.text(''+line[0], 0, 0)

      oled.show()

### Step 3
Now that we have both library in the esp32 we are going to test if it works.
Connect the esp32 with your computer and run the above code with Ssd1306.py and oLed.Control.py installed in the esp32

Connect the OLED display to ESP32 where:

      GND connected to esp32 GND
      VCC connected to esp32 3.3V
      scl connected to esp32 Pin 22
      sda connected to esp32 Pin 21

Open a new file run these lines:

      import oLedControl as o
      import time

      while True:
        line = ['','','','']
        line[0] = 'Hello'
        line[1] = 'I am '
        line[2] = 'Vincent'
        o.display_(line)
        time.sleep(3)
        line = ['','','','']
        line[0] = 'I am'
        line[1] = 'New'
        line[2] = 'to Programming 1'
        o.display_(line)
        time.sleep(3)

o.display_(line) is used to execute the display of OLED. line is used as a list to store the information as strings

If it worked, you should be able to see the OLED display

        Hello
        I am
        Vincent
 for 3 seconds followed by

        I am
        new
        to Programming 1
and then it will loop back to

        Hello
        I am
        Vincent

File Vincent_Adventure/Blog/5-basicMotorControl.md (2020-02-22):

# Basic Motor Control
## Introduction
Now that we have successfully flashed the esp32, we will try to use the esp32(micropython)(Thonny) to control a tracked vehicle

### Components needed for the setup
* [Tracked Vehicle (With 12V DC motor)](https://www.aliexpress.com/item/32821691519.html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,searchweb201602_2,searchweb201603_53)
* [Esp32](https://github.com/hamtamSP/JAV2/blob/master/Vincent_Adventure/Blog/3-esp32.md)
* L298N H-bridge
* Dupont wires
* 2 (3.7V 3000mAh 18650 Lithium-ion Battery)
* Lithium Ion battery holder
* Boost Converter

### Motor control
1. Firstly, ensure that Esp32 is [flashed](https://github.com/hamtamSP/JAV2/blob/master/Vincent_Adventure/Blog/3-esp32.md).
2. Connect the circuit according to the schematic below
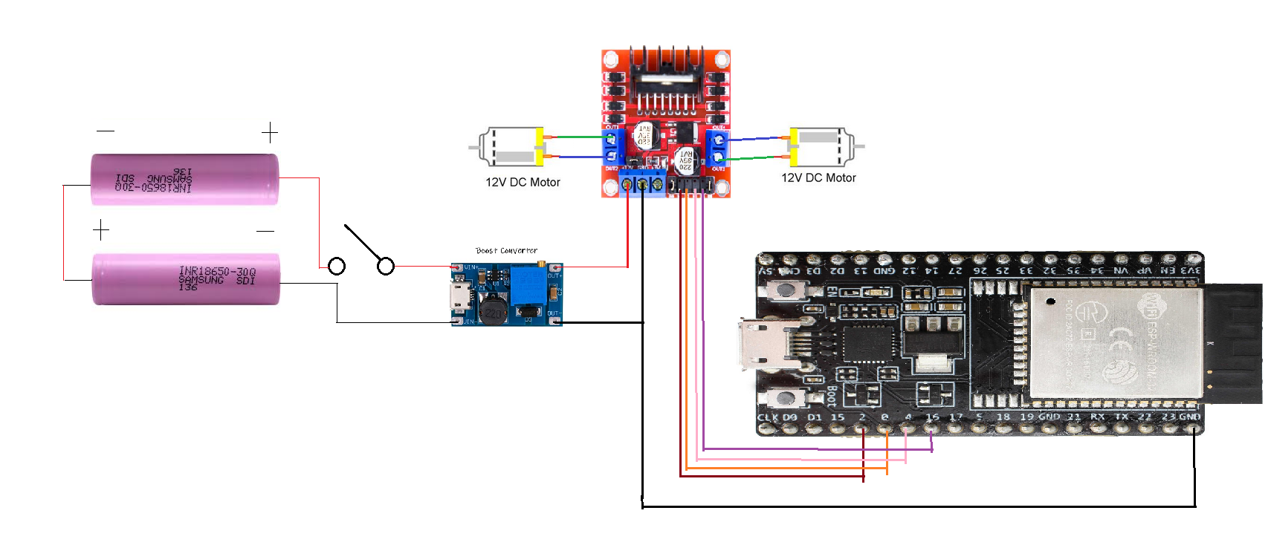
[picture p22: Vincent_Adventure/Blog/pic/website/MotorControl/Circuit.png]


        (Be Careful with lithium ion batteries, use a digital multimeter to find where is the positive side and the negative side)      
3. Adjust the Boost Converter such that it outputs 12v when you measure the voltage across Vout+ and Vout-
4. Open Thonny ,Connect the ESP32 via USB Cable to your computer and open a new file
5. Upload this code, save and run
        from machine import Pin
        import time
        # =====================================================================
        int1 = 2  #Brown
        int2 = 0  #Orange
        int3 = 4  #Pink
        int4 = 16 #Purple

        enA = 15
        enB = 17
        # =====================================================================
        motor1a = Pin(int1,Pin.OUT)
        motor1b = Pin(int2,Pin.OUT)
        motor2a = Pin(int3,Pin.OUT)
        motor2b = Pin(int4,Pin.OUT)
        pulseA = Pin(enA,Pin.OUT)
        pulseB = Pin(enB,Pin.OUT)
        pulseA(1)
        pulseB(1)
        # =====================================================================
        def fwd():     
            motor1a(0)
            motor1b(1)
            motor2a(0)
            motor2b(1)
        def stop():    
            motor1a(0)
            motor1b(0)
            motor2a(0)
            motor2b(0)
        def back():
            motor1a(1)
            motor1b(0)
            motor2a(1)
            motor2b(0)
        def rotationLeft():
            motor1a(0)
            motor1b(1)
            motor2a(1)
            motor2b(0)
        def rotationRight():
            motor1a(1)
            motor1b(0)
            motor2a(0)
            motor2b(1)
        def rest():
            stop()
            time.sleep(1)
        # =====================================================================
6. Use the Repl from Thonny to run the Motors
For Example:
        fwd()
7. Change the motor output accordingly, motor1a and motor1b must be in opposite Boolean logic, motor2a and motor2b must be in opposite Boolean logic,
8. After doing adjustments, save a copy of the file into ESP32 and label it as
        MotorControl.py

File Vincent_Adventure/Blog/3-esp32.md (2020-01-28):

# Week 4
## Micro Python using ESP 32
### Firmware Type
We are using a ES32-WROOM-32D   
TXS0108 (5V to 3.3V converter)

### Esp32
We got the ESP32 from [Aliexpress](https://www.aliexpress.com/item/32864722159.html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,searchweb201602_2,searchweb201603_55).
### Setup of ESP32
When you get your hands on a brand new ESP32, you would realize that you cannot write any code into it. That is because ESP32 run through machine language. In order for the ESP32 to run micropython, we will need to flash it. Please refer to [How to Flash ESP32](https://randomnerdtutorials.com/flashing-micropython-firmware-esptool-py-esp32-esp8266/) to flash and for [Firmware for ESP32](http://micropython.org/download#esp32) firmware download.

#### Steps:
    Step 1: Download python 3.7 (Can skip if you have Python 3.7 Installed)
[Python download](https://www.python.org/downloads/)

    Step 2: Install esptool from using command prompt

(For windows 10):   
Go to search bar and type :     
command prompt    
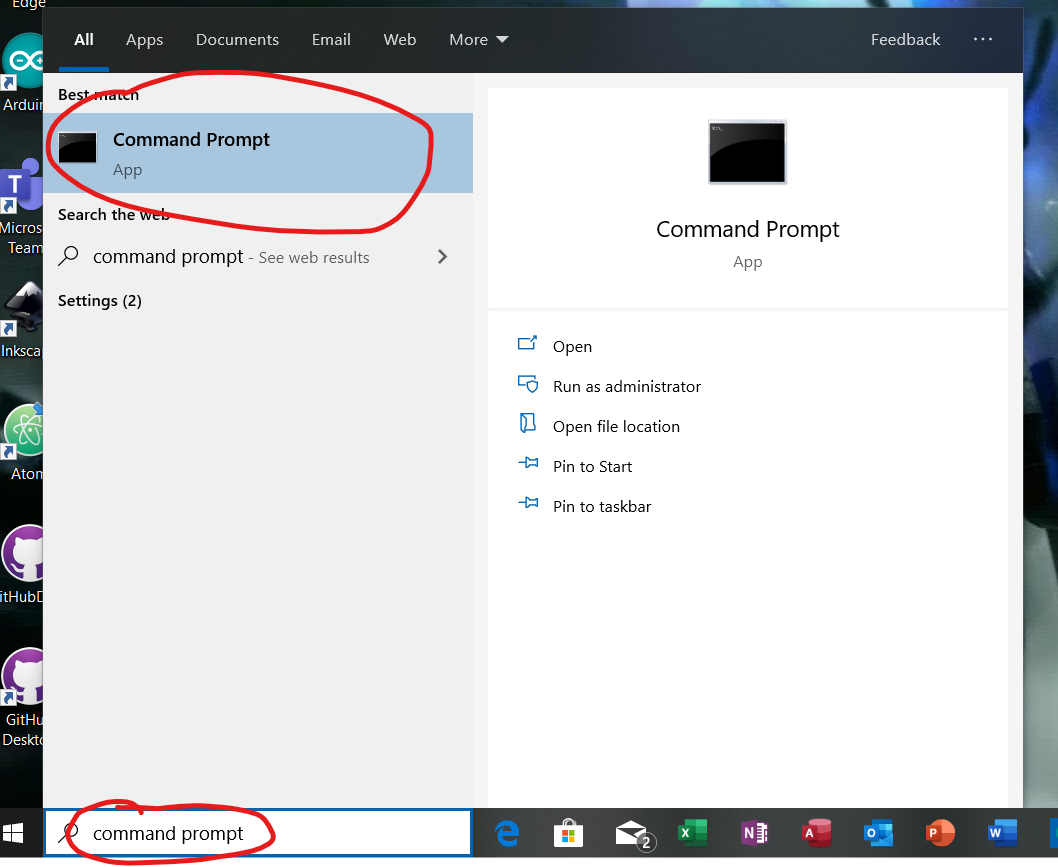
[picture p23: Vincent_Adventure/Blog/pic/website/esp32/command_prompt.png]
  
Type:   
pip install esptool
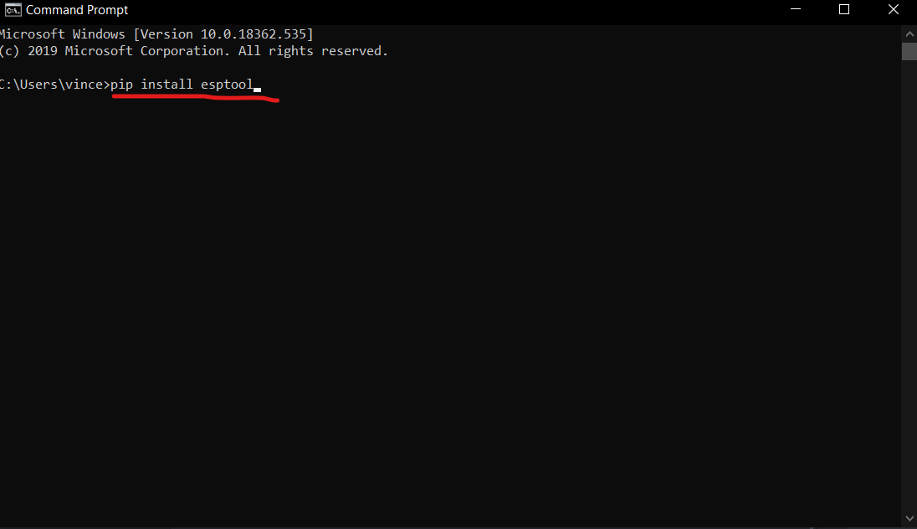
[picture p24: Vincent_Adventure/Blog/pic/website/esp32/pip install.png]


Check if esptool is downloaded, type:   
esptool   
or    
esptool.py
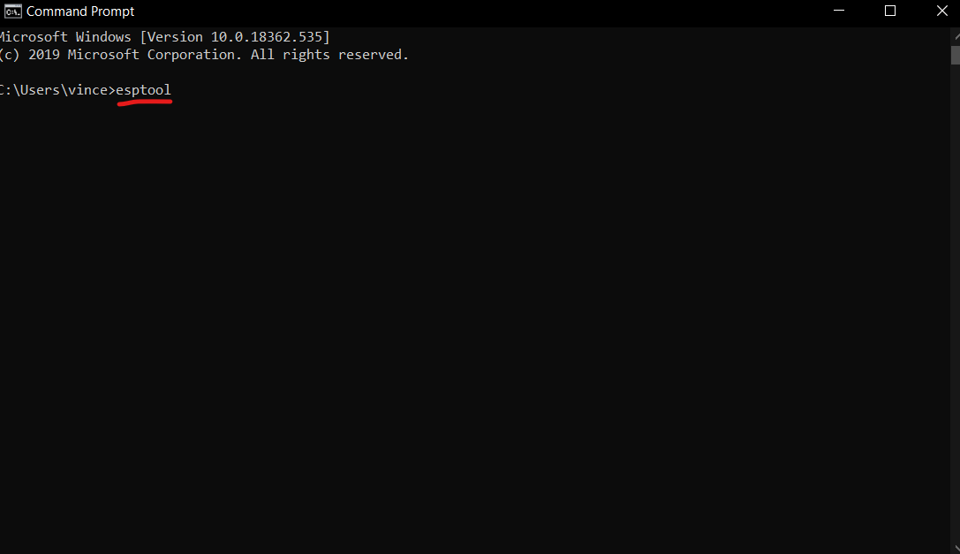
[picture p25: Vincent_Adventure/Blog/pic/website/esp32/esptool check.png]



    Step 3: Download Esp32 Firmware

Go to [Firmware for ESP32](http://micropython.org/download#esp32) and
download firmware. I will being using the wifi flash for esp32


While downloading, connect esp32 to your computer.   
Open thonny>run>selected interpreter>go to port and take note of the port.

My esp32 is connect to com6   

hold the boot button, Open command prompt and type:    

    esptool --chip esp32 --port com6 erase_flash



By now, the flash file should be downloaded, copy the file name:


Go to command prompt and type:

    esptool --chip esp32 --port com6 --baud 460800 write_flash -z 0x1000 esp32-idf3-20191220-v1.12.bin
# Done!

## Run some test  
So to test if the esp32 has been flashed properly, we are going to run a simple experiment of led blink

Open Thonny> create new file> copy and paste the [code]()

    from machine import Pin
    import time
    # =====================================================================

    led = Pin(2,Pin.OUT)
    while True:
    led(1)
    time.sleep(0.5)
    led(0)
    time.sleep(0.5)

prepare an Led and  one 330 ohm resistor

* place the resistor such that it connects pin 2 of esp32
* connect the long leg of the led to the other end of the resistor
* connect the short leg of the Led to ground of the esp32



Reference links:  
[How to Flash ESP32](https://randomnerdtutorials.com/flashing-micropython-firmware-esptool-py-esp32-esp8266/)   
[Firmware for ESP32](http://micropython.org/download#esp32)

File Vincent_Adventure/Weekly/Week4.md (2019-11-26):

# Week 4
## Micro Python using ESP 32
### Firmware Type
We are using a ES32-WROOM-32D   
TXS0108 (5V to 3.3V converter)

### Esp32
We got the ESP32 from [Aliexpress](https://www.aliexpress.com/item/32864722159.html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,searchweb201602_2,searchweb201603_55).
### Setup of ESP32
When you get your hands on a brand new ESP32, you would realize that you cannot write any code into it. That is because ESP32 run through machine language. In order for the ESP32 to run micropython, we will need to flash it. Please refer to [How to Flash ESP32](https://randomnerdtutorials.com/flashing-micropython-firmware-esptool-py-esp32-esp8266/) to flash and for [Firmware for ESP32](http://micropython.org/download#esp32) firmware download.

#### Steps:
    Step 1: Download python 3.7 (Can skip if you have Python 3.7 Installed)
[Python download](https://www.python.org/downloads/)

    Step 2: Open command prompt in your computer
(For windows 10): Go to search bar and type :     
command prompt    
  

    Step 3:

links:  
[How to Flash ESP32](https://randomnerdtutorials.com/flashing-micropython-firmware-esptool-py-esp32-esp8266/)   
[Firmware for ESP32](http://micropython.org/download#esp32)

# Things to do
* write up on how to setup ESP32 using window system
* what is a flash
* Use LAN as a common platform for communicating with the ESP32.
* flowchart
* purchase
* voltage divider

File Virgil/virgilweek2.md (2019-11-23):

# JAV²

Author: Virgil D'souza

## Programming a game on microbit

This week, I was tasked on creating a 'Space Invaders'
game using microbit. It was a very interesting
experience as it allowed me to discover the different
uses of microbit and Python programming.

I was able to code the game with success,
with an objective of avoiding the aliens.
Once the player hits an alien, the game is over.

### The code

from microbit import *<br>
import random

ship = 2<br>
a1 = random.randint(0, 4)<br>
a2 = 0

while True:<br>
    display.clear()<br>
    display.set_pixel(ship, 4, 5)<br>
    display.set_pixel(a1, a2, 9)

    a2 = a2 + 1
    if a2 > 4:
        a1 = random.randint(0, 4)
        a2 = 0

    if button_a.is_pressed():
        ship = ship - 1
    if button_b.is_pressed():
        ship = ship + 1

    if ship == a1 and a2 == 4:
        break

    sleep(250)

display.scroll("GAME OVER!", loop = True)

The code uses the microbit and random libraries
in micropython. According to the code,
Button A moves the ship left and Button B
moves the ship right. The randint() function
serves as a random generator for the position
of the alien.

### Problems

A problem that I encountered while coding the game
was how to prevent a program glitch when the alien
went out of range. To remedy this, I used an if
statement to reset the value of y to 0 and
added in another randint() function to regenerate
a new x value.

Another problem I encountered was how to
regenerate the alien. Using the same if
statement mentioned earlier, I called a new
randint() function to generate a new x value
and effectively, a regenerated alien.

### Pro Tip

A pro tip I would suggest is to use short sleep time
so that the ship reacts quickly to button press.

## Thonny Tutorial

https://www.youtube.com/watch?v=TK16sAk1sIk

This is a tutorial for Thonny IDE that I would
personally recommend as it covers the very basics
sufficient to get started.

It also touches on how to output values using
the text editor and shell.

## Python Programming for Beginners

https://www.youtube.com/watch?v=D48iCw3WWpI

This is a tutorial I would recommend for those
who are new to Python. It covers basic arithmetic
operations and data types. It gives tips on how
to declare variables. It also has exercises at
the end to test and refresh what you have learnt.

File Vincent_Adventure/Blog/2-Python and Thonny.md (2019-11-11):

# Micro Python
I have been learning python for a while now. Micro python is similar to python where the code structure is more or less identical to Python
## Learning Python
Link: https://www.youtube.com/watch?v=rfscVS0vtbw

I personally recommend this link to start on learning Python because he give u examples to try an apply so that I can see for myself if the code works, then understand how the flow of the code works. He covers almost all the basics of python. By providing the basics, it is up to me to continue to search for more library to explore more of what python can do. The downside of this video link is that it is a 4 hour duration tutorial. I have a short attention spend and I believe that there are many of you, who are reading this page, who have similar problems, we are not able to learn consistently for 4 hours due to time constraint etc. So I would recommend separating the video into 4 or 8 sections, making a 30 mins to 60 mins per section. This learning system might not be the most efficient for most of the people a who want to learn Python, but at least for me, it gets the jobs done.

## Thonny
#### links:
* [Python IDE Thonny](https://www.youtube.com/watch?v=lWaCl0WjNZI)
* [Thonny: IDE For Teaching Beginners](https://www.youtube.com/watch?v=JLOOWVwDftg)

There are very few tutorials in regards in using Thonny. But since Thonny uses MicroPython/python as their writing language learning the basics of python will more or less get you to where u can start off exploring more into Thonny. As for the youtube tutorials for Thonny, I would recommend watching [Python IDE Thonny](https://www.youtube.com/watch?v=lWaCl0WjNZI). It is a good that the teacher in the video shows what shortcut buttons in which you can use to boost your efficiency of your experience in Python Programming. There are times where you might get what he is doing, don't worry, I also do not get it the first time. just replay the video as few more times and try to understand it. Soon, you would get it. The tutorial is relatively short but it contains all the basic skills to learn to kick start into Thonny. 

## Code style
Whenever I write a code, I tend to put sections of my code in functions, with a name related to what the code does. By doing this, I am able to debug my code by searching through the list of functions instead of searching through the entire code. However, writing the code in functions increase the memory storage of the device, which is not efficient in terms of device memory usage. To add on, I am using up too many lines to write the code, which will slow the configuration of the device I use. to improve, I can short the lines by having a better algorithm or squeeze all the lines to one line. I priorities on readability over speed, so the only way I can increase the speed is by creating a better algorithm.
Due to the fact that I have a short memory, I comment my codes as much as possible. It is a good practice adopt by all coders.

## Space Invader Game!
Now, I will be putting what I have learn about MicroPython and BBC Microbit to a test by replicating a traditional game called
For this game, I will be using [BBC Microbit](https://microbit.org/) hardware, which comes with a built in 5x5 led matrix.
BBC Micro is design for small projects, in other words there many built in actuators like LED and sensors but it have very low memory. for this game, I will design the gam in such that player only have dodge the alien, but doesn't have to shoot them down. I will be using Thonny as my IDE to write and upload code to the BBC Microbit.

This is my Source Code
* [Space Invader](https://github.com/hamtamSP/JAV2/blob/master/Vincent_Adventure/Weekly/Source_code/SpaceInvader.md)

## Reflection of Space Invader Game

The game was build successfully. The problems I faced was that the BBC Microbit have less memory than that of the other hardware I used in my previous projects. With the restriction of limited memory I cannot create more functions for more clarity, as each function was consume much more memory. Well to solve this problem, I have to squeeze different codes functions together to minimize the memory spaced used. Then, to solve clarity of code, I commented as much as possible. Another problem I face is the declaration of global and local variable. I am a adequate in writing code and programs. The course in which I am currently studying helped me learn the basics of coding like, declaring variables, loops, storing etc. I am not so familiar with declaring of local and global variable. I tend to get mixed up with the variables. There are a few solutions to this particular problem that I am facing, where I just squeeze all the codes into on functions, so I do not have to worry about redefining variables. However, based on past experience, I would try to avoid using that solution as it will make me confused as I continue writing. the solution I used to solve the variables problem is that I draw the flow and what variable the local to which function etc.

## Advises
To all the people who are new to coding or already starting coding, know what you want to do and understand the flow of the coding logic. Make sure to comment major lines as much as possible. And lastly, take note and understand what went wrong with the code in your attempts.

##### NO ONE GETS THE CODE WORKING PERFECTLY WITHIN A FEW TRIES.
##### DON'T GIVE UP! KEEP ON TRYING!

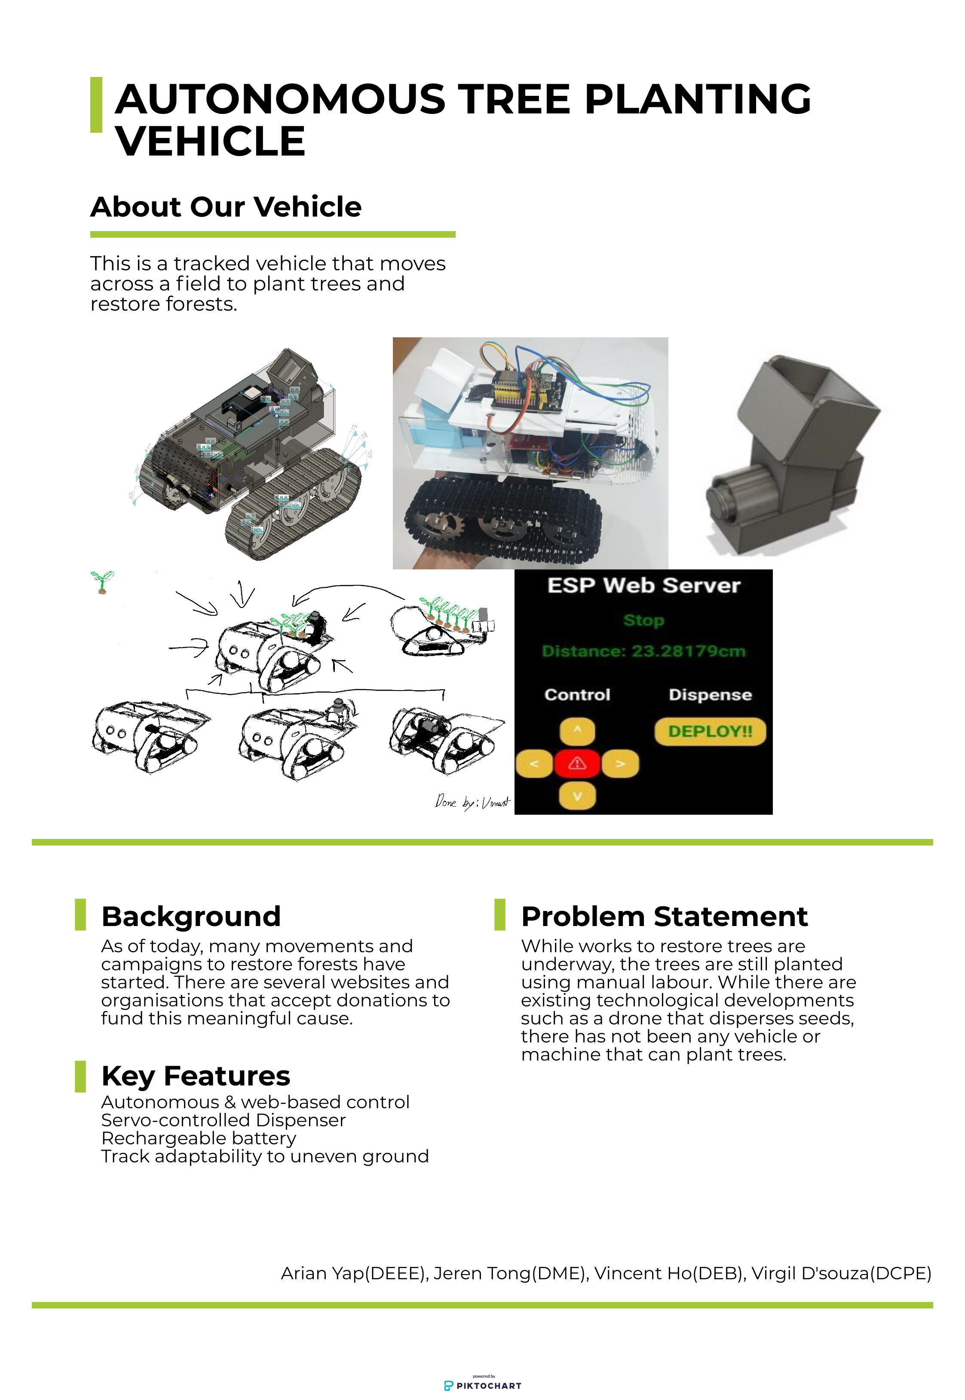
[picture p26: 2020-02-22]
Virgil/EA Final Poster.png

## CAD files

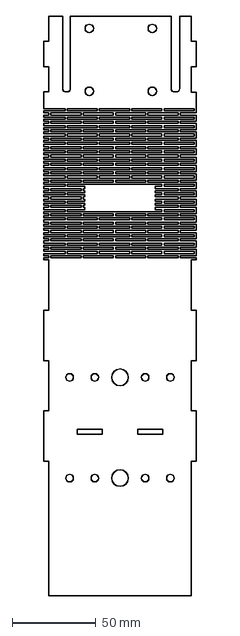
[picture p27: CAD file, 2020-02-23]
Vincent_Adventure/Blog/assembly Files/living hinge+body assembly.dxf
91.0 x 345.0 mm

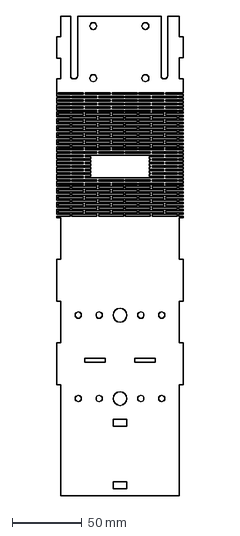
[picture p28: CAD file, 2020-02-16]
Vincent_Adventure/SideTrackXPloration/designs/holder/main.dxf
91.0 x 345.0 mm

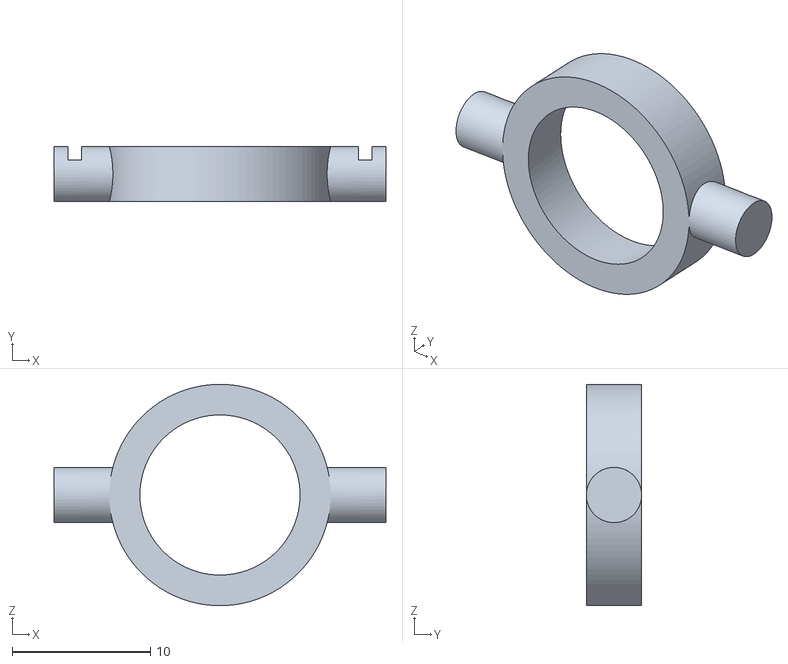
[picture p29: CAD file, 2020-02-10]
Vincent_Adventure/SideTrackXPloration/designs/case 2-2.stl
24.0 x 4.00 x 16.0

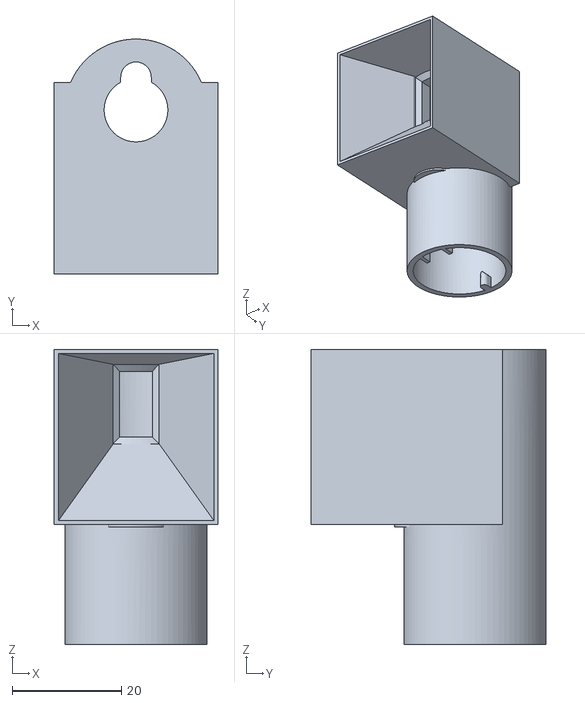
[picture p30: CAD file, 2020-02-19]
Vincent_Adventure/SideTrackXPloration/designs/holder/TUBE2.stl
30.0 x 43.0 x 54.0

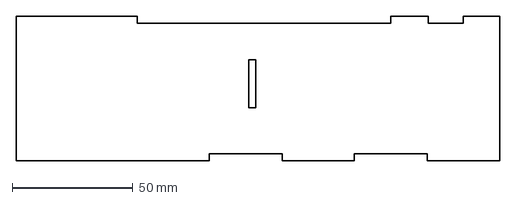
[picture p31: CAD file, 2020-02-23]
Vincent_Adventure/Blog/assembly Files/side of vehicle(without holes).dxf
200.0 x 60.0 mm

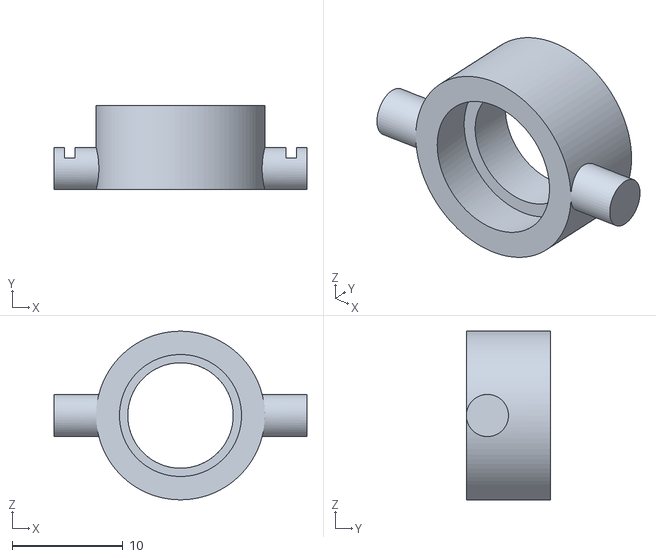
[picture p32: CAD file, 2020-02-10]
Vincent_Adventure/SideTrackXPloration/designs/case 2-2-2.stl
22.8 x 7.60 x 15.2

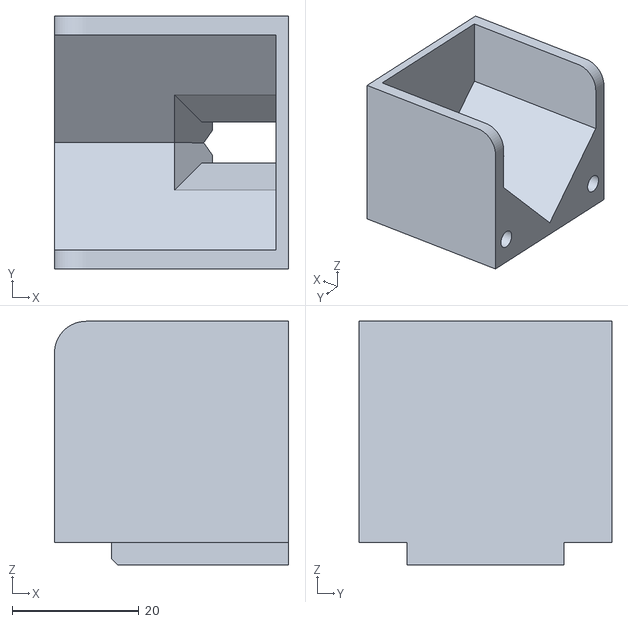
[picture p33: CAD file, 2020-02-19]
Vincent_Adventure/SideTrackXPloration/designs/holder/body2.stl
37.0 x 40.0 x 38.5

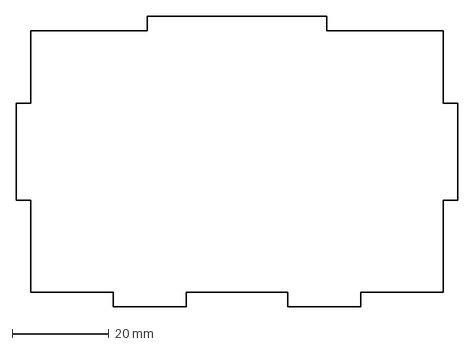
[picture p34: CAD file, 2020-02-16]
Vincent_Adventure/Blog/assembly Files/middle seperation.dxf
91.0 x 60.0 mm

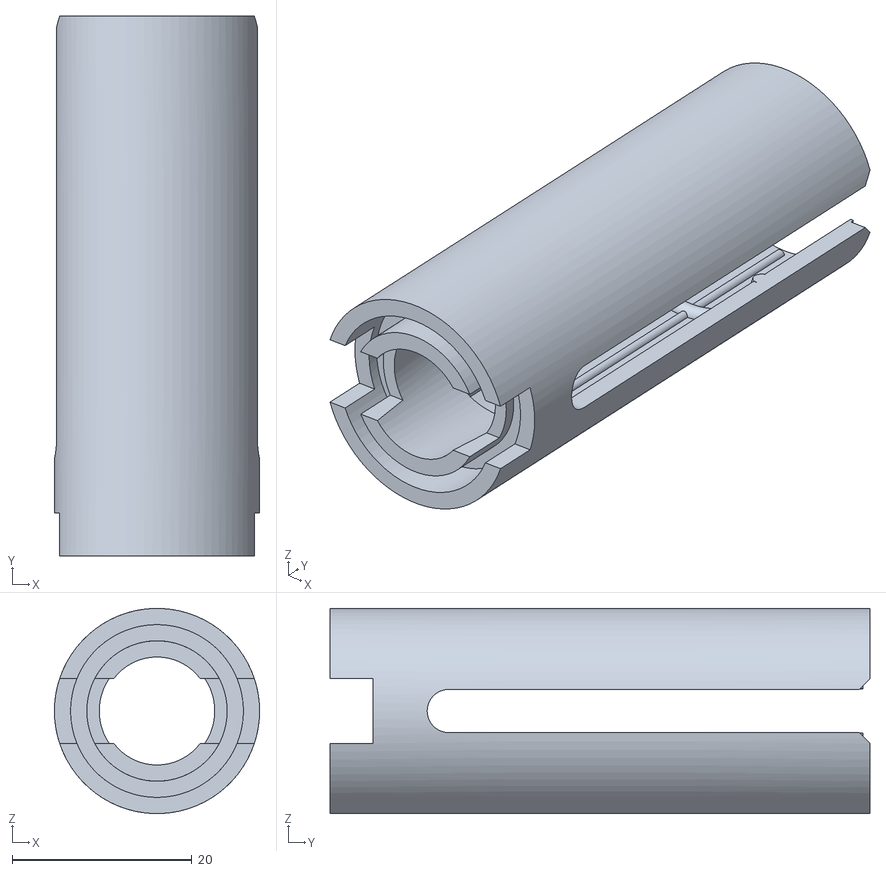
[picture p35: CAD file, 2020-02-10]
Vincent_Adventure/SideTrackXPloration/designs/case 2-1-2.stl
22.8 x 60.0 x 22.8

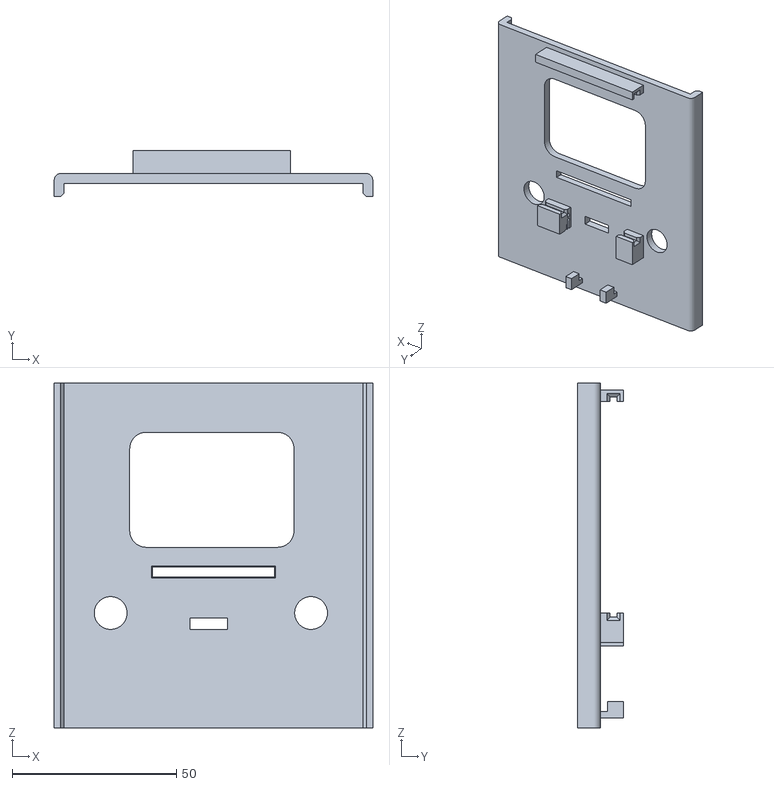
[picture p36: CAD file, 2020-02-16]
Vincent_Adventure/SideTrackXPloration/designs/holder/espStore.stl
97.0 x 14.0 x 105.0

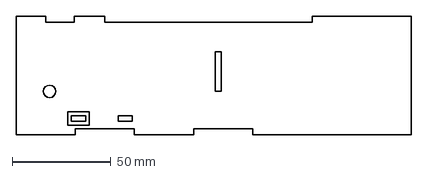
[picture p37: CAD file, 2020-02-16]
Vincent_Adventure/Blog/assembly Files/side of the vehicle.dxf
200.0 x 60.0 mm

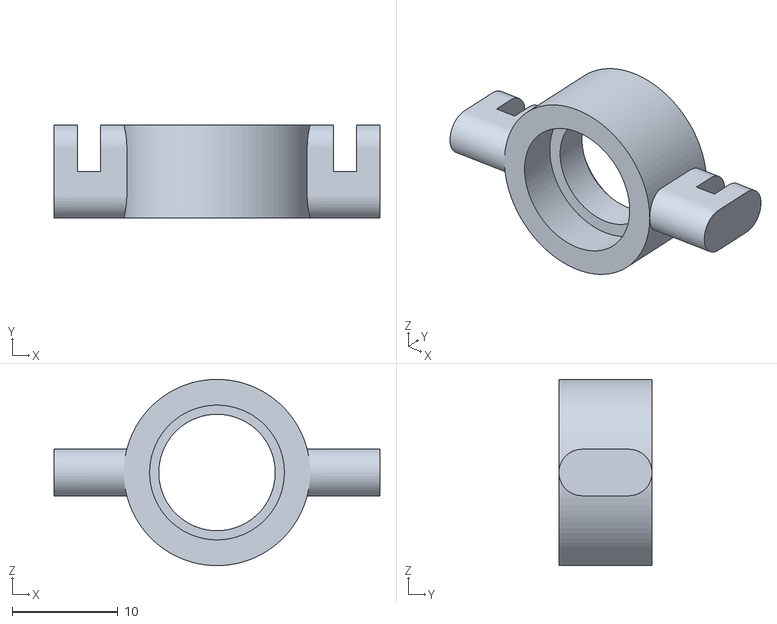
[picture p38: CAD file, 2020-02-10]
Vincent_Adventure/SideTrackXPloration/designs/case 2-2-4.stl
30.8 x 8.80 x 17.6

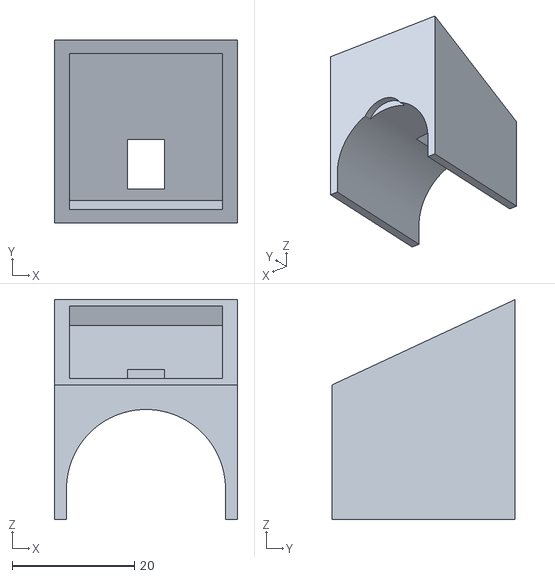
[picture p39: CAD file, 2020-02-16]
Vincent_Adventure/SideTrackXPloration/designs/holder/holder.stl
30.0 x 30.0 x 36.0

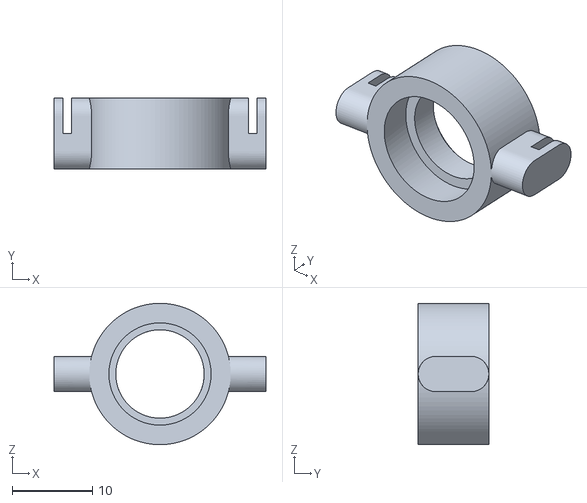
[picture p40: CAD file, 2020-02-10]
Vincent_Adventure/SideTrackXPloration/designs/case 2-2-3.stl
26.4 x 8.80 x 17.6

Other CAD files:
Vincent_Adventure/SideTrackXPloration/designs/holder/beanstack.stl
Vincent_Adventure/SideTrackXPloration/designs/case 1.stl
Vincent_Adventure/SideTrackXPloration/designs/case 2-1.stl
Vincent_Adventure/SideTrackXPloration/designs/holder/tube.stl
Vincent_Adventure/SideTrackXPloration/designs/holder/cone.stl
Vincent_Adventure/SideTrackXPloration/designs/holder/drill.stl
Vincent_Adventure/SideTrackXPloration/designs/holder/holder-1-female-1.stl
Vincent_Adventure/SideTrackXPloration/designs/holder/holder-1-female-2.stl
Vincent_Adventure/SideTrackXPloration/designs/holder/holder-1-female-3.stl
Vincent_Adventure/SideTrackXPloration/designs/holder/holder-1-female-4.stl
Vincent_Adventure/SideTrackXPloration/designs/holder/holder-1-male-1.stl
Vincent_Adventure/SideTrackXPloration/designs/holder/holder-1-male-2.stl
Vincent_Adventure/SideTrackXPloration/designs/holder/holder-1-male-3.stl
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

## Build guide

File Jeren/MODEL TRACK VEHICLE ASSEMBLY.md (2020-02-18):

# Assembling a model tracked vehicle
##### Week 3
***
## Introduction
For this week, we were given an unassembled tracked vehicle so that we can assemble. The parts will eventually become the base of our actual tracked vehicle after modifications.
***
What we used for this week:
* Mini T100 Tracked Tank Chassis (Silver with 12V motor)
***
https://github.com/SmartArduino/ESPboard/blob/master/T-Series%20Tank%20Assembly.pdf

We followed this guide to assemble the driving and bearing wheel of the vehicle.
***
https://www.youtube.com/watch?v=0Bmx-a5FjmA&feature=youtu.be

We found a video for installing the tracks of the video.
***
https://www.youtube.com/watch?v=od4h0dyjrQA&feature=youtu.be

But in the end we found a video to assemble the whole tank, which make the other 2 guide kind of useless.

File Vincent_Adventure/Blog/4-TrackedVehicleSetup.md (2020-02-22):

# Setup of Tracked Vehicle
## Introduction
We bought a [Tracked Vehicle](https://www.aliexpress.com/item/32821691519.html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,searchweb201602_2,searchweb201603_53) from AliExpress, we need to assemble it. There is a [default assembly](https://github.com/SmartArduino/ESPboard/blob/master/miniT100Instruction.pdf) provided by the supplier

    Step 1: Keep Track of your inventory
 It is a good practice to keep track of what u have received from online purchase, so as for us, we took picture of what we have.
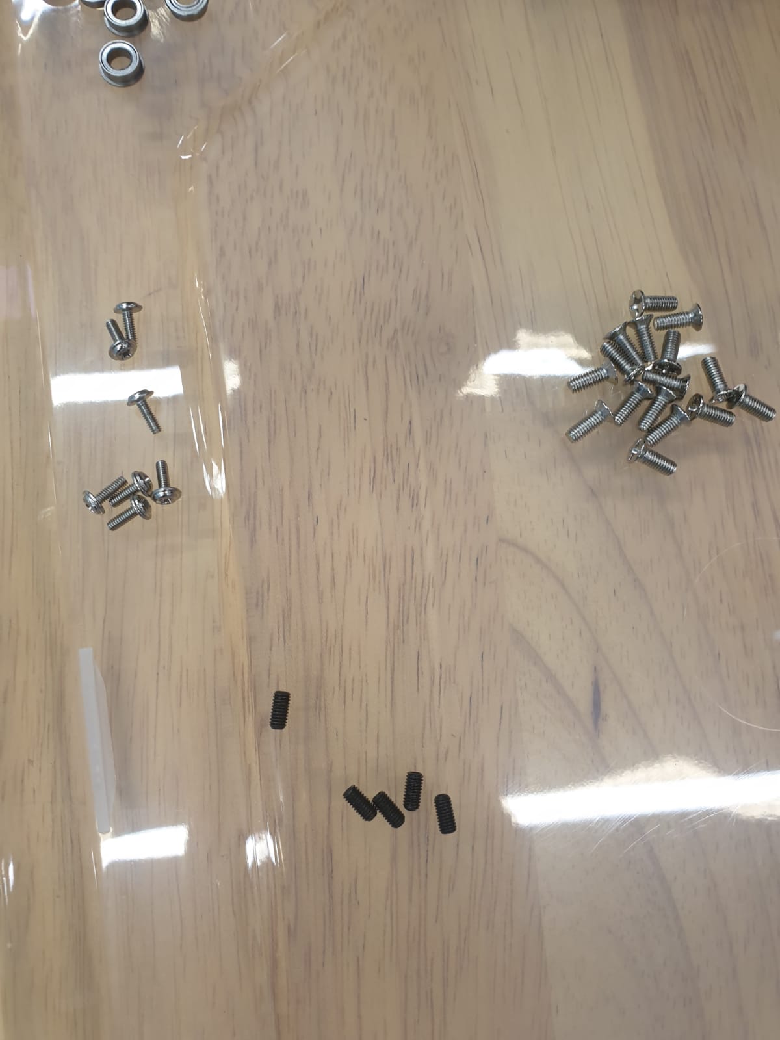
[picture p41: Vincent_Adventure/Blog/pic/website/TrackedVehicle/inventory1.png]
 
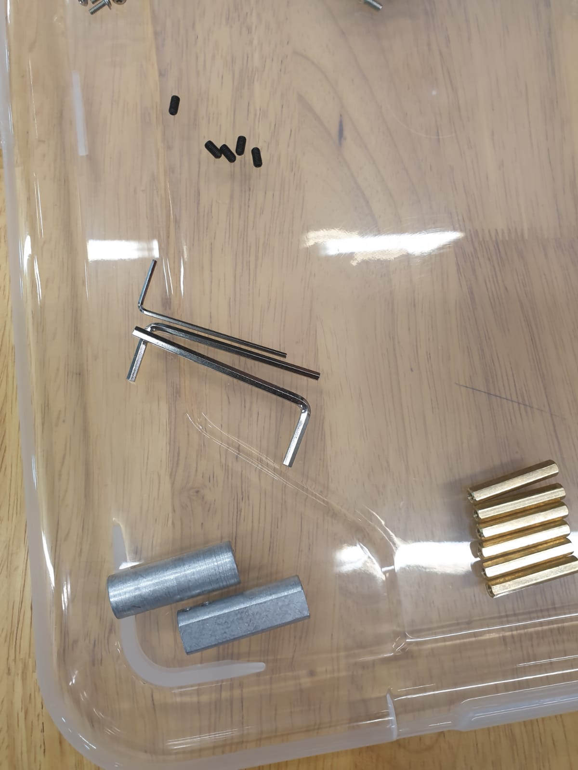
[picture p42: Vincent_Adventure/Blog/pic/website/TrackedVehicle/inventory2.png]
 
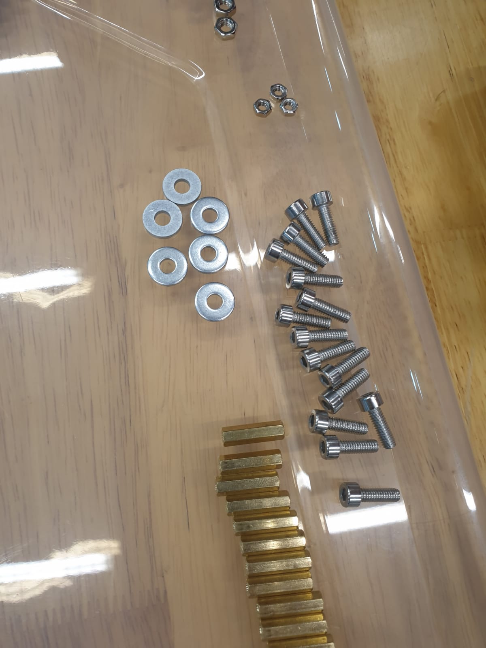
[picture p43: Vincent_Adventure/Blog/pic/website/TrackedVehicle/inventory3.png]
 
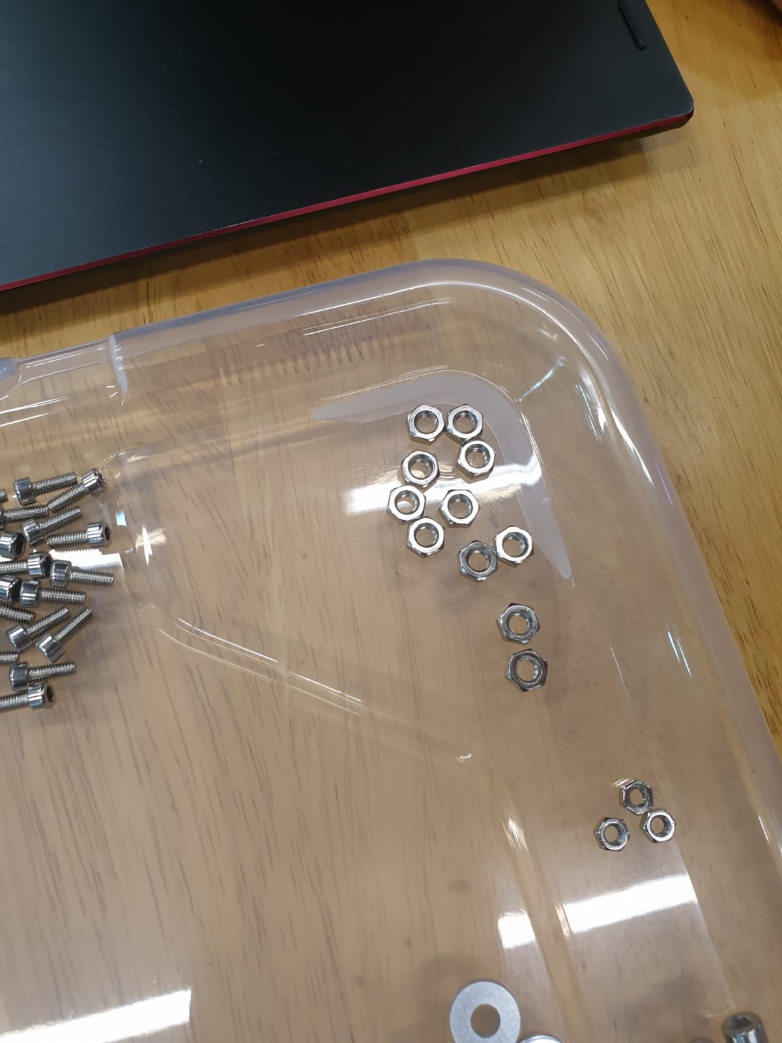
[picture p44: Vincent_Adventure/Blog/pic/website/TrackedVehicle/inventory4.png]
 
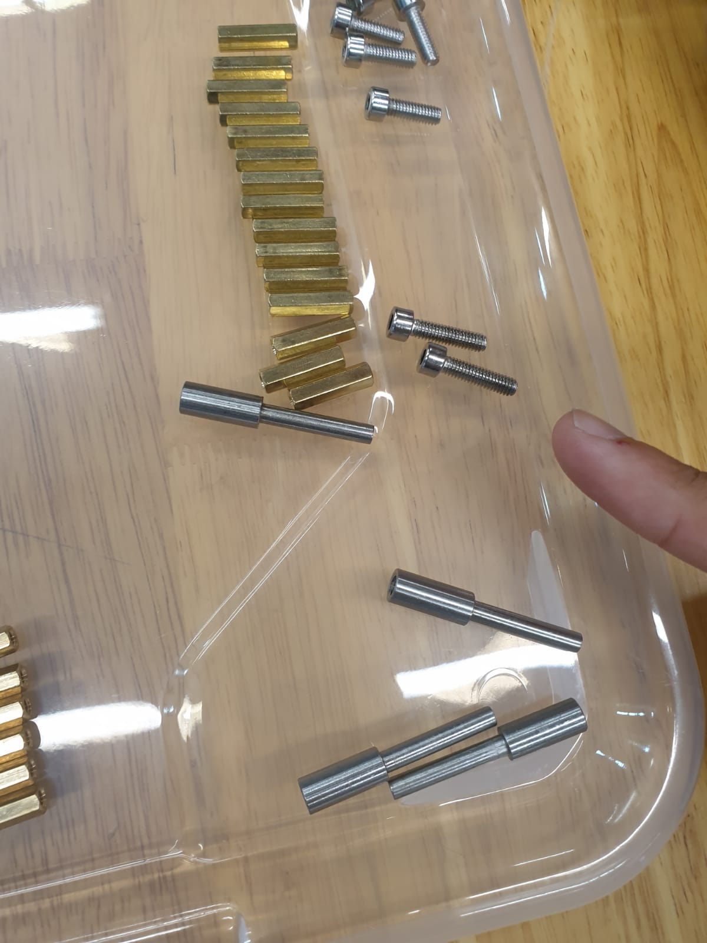
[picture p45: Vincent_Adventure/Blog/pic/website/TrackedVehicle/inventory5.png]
 
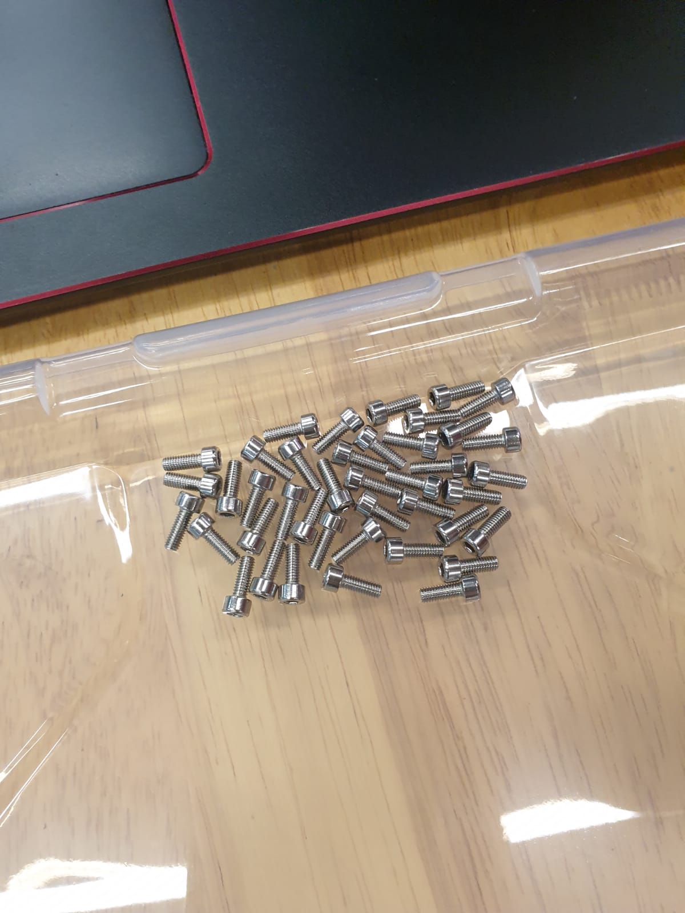
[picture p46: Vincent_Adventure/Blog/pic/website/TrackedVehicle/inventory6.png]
 
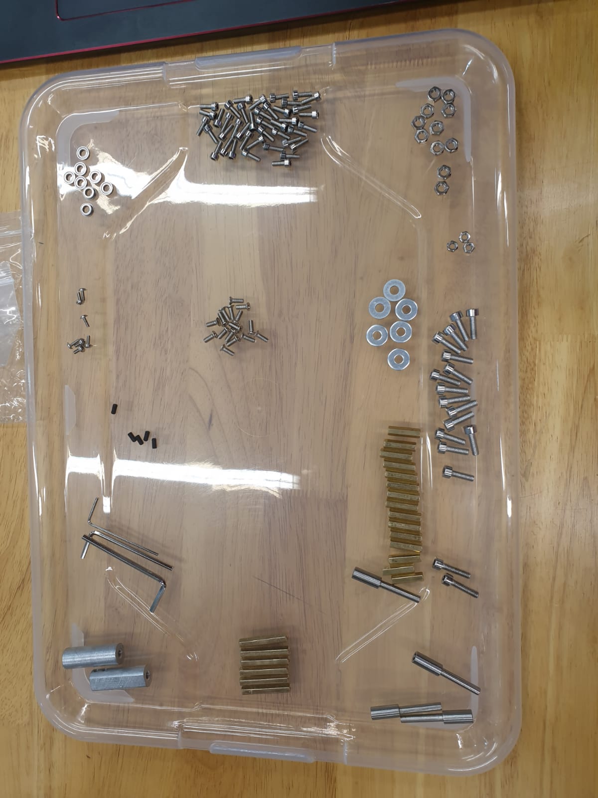
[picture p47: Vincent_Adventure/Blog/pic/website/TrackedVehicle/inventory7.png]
 
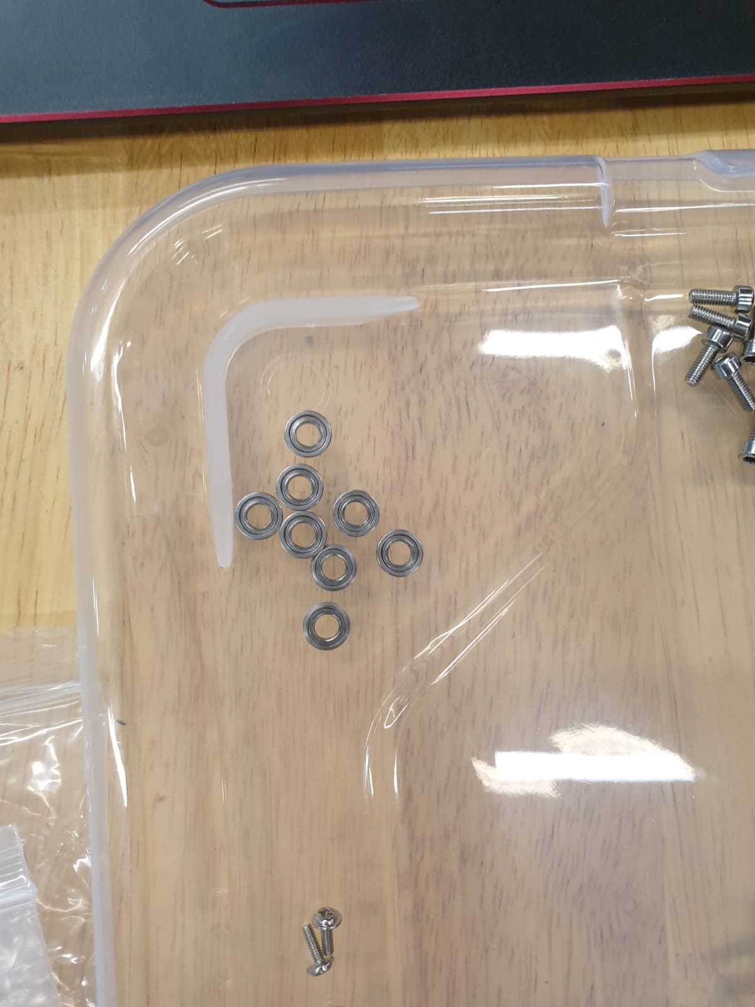
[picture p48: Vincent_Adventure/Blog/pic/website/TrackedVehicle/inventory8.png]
 
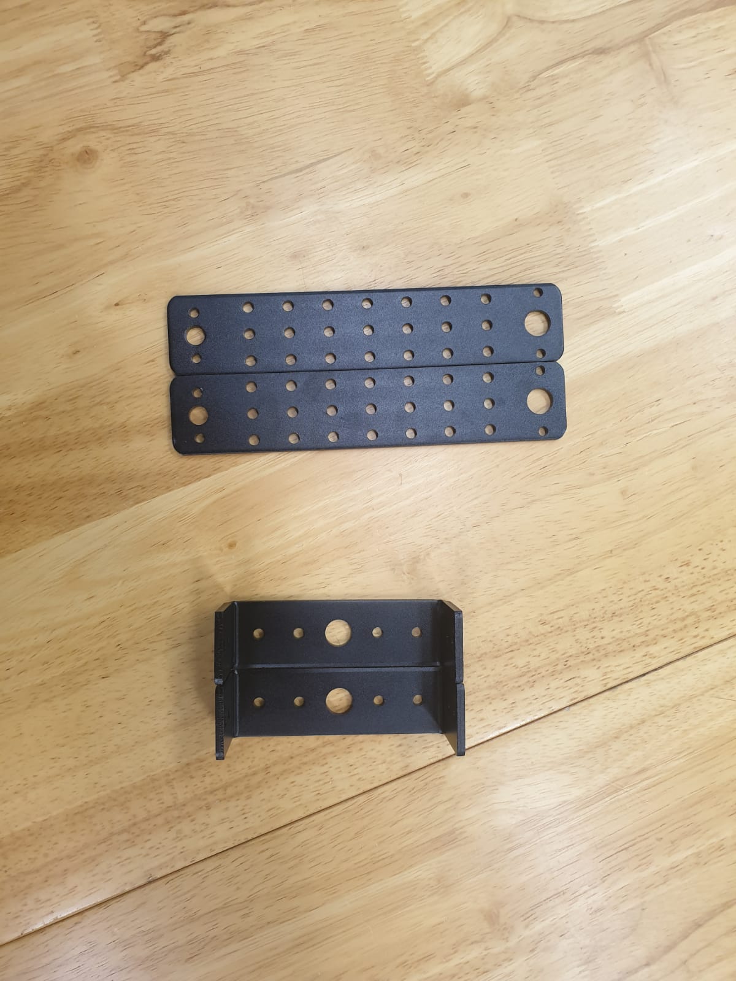
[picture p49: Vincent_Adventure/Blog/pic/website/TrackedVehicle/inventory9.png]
 

    Step 2: Assembly
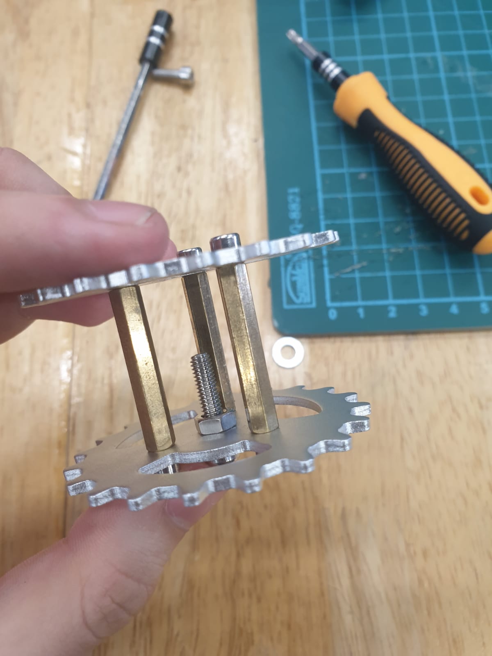
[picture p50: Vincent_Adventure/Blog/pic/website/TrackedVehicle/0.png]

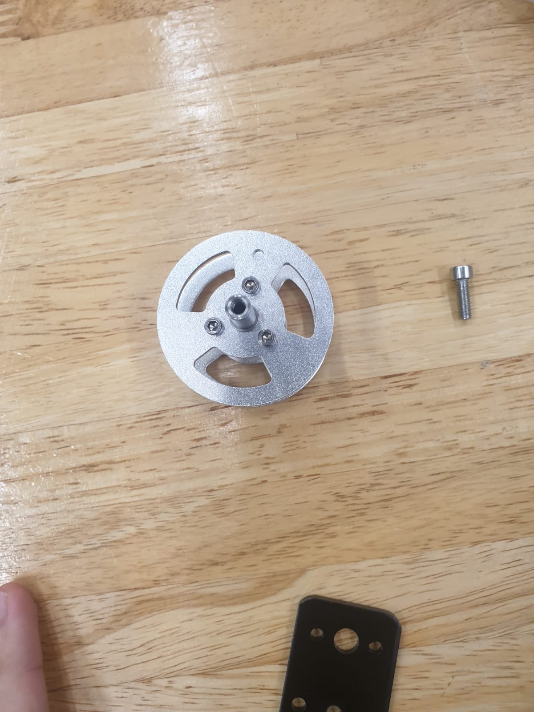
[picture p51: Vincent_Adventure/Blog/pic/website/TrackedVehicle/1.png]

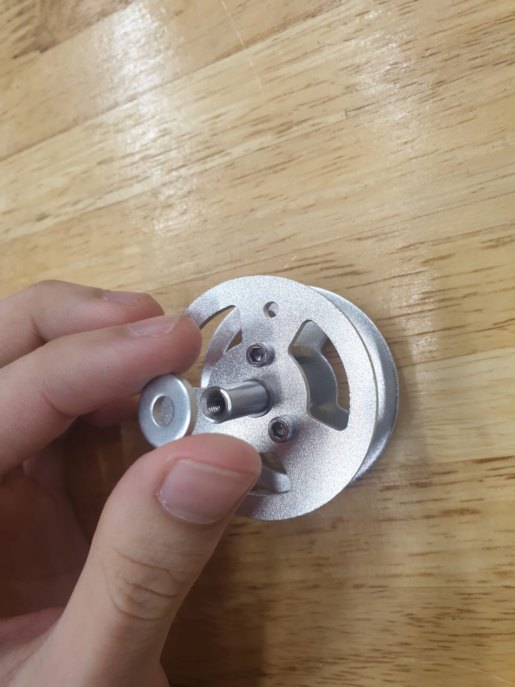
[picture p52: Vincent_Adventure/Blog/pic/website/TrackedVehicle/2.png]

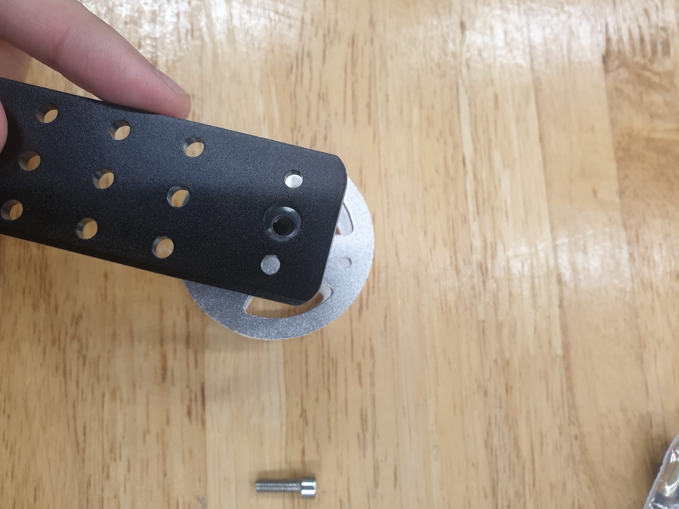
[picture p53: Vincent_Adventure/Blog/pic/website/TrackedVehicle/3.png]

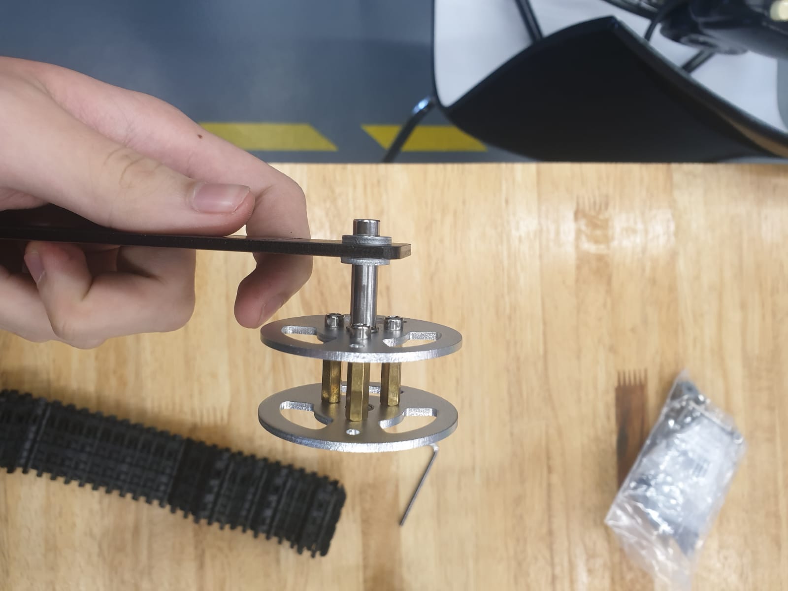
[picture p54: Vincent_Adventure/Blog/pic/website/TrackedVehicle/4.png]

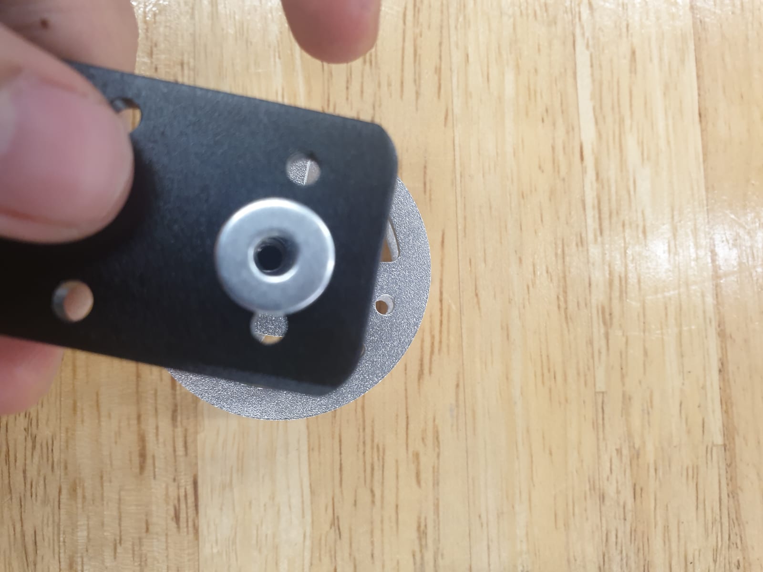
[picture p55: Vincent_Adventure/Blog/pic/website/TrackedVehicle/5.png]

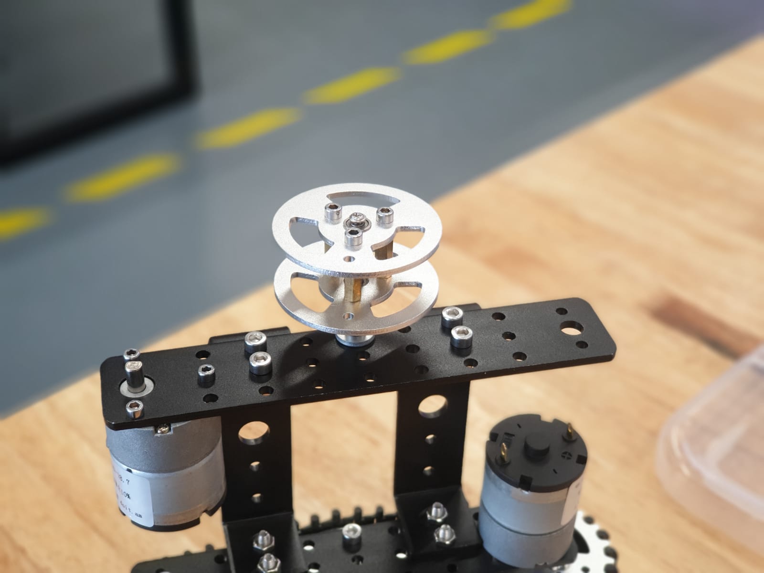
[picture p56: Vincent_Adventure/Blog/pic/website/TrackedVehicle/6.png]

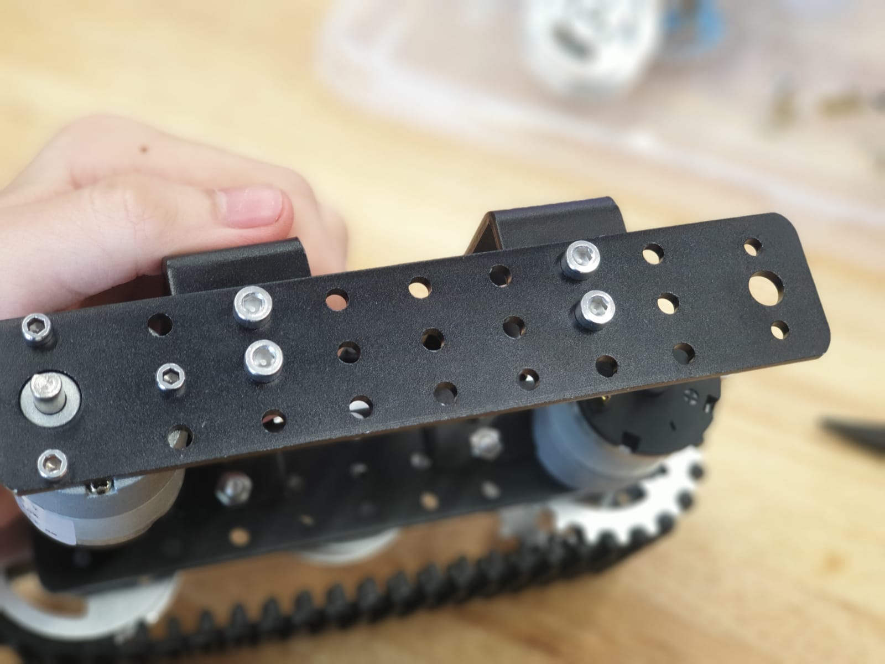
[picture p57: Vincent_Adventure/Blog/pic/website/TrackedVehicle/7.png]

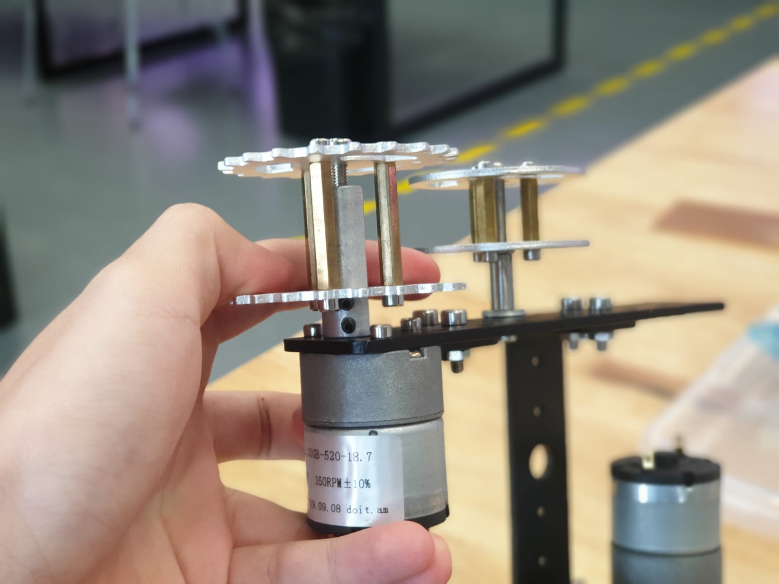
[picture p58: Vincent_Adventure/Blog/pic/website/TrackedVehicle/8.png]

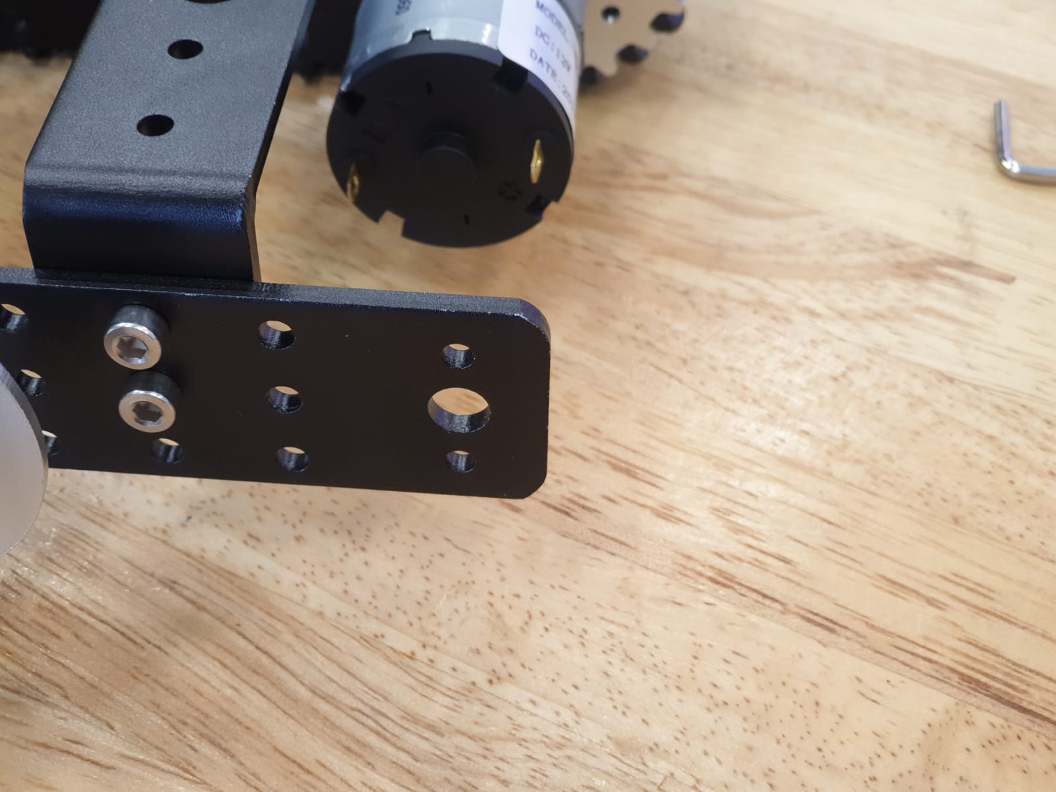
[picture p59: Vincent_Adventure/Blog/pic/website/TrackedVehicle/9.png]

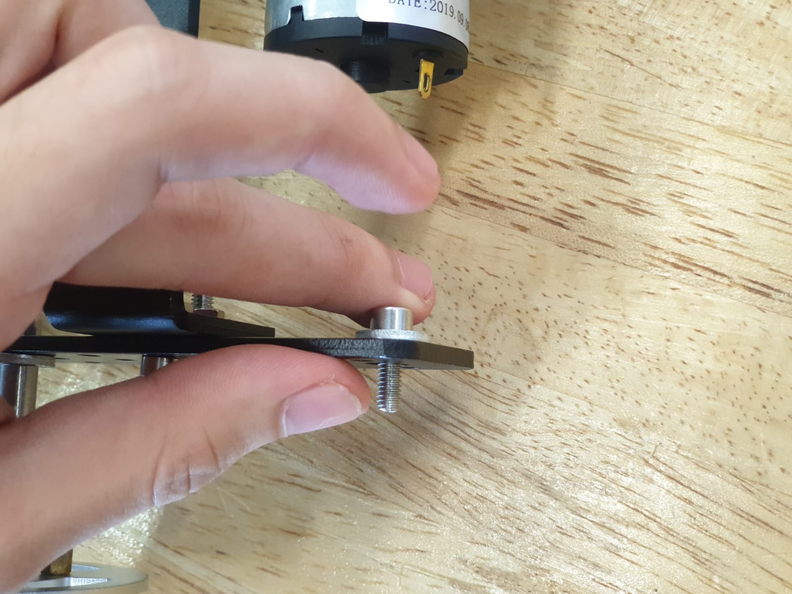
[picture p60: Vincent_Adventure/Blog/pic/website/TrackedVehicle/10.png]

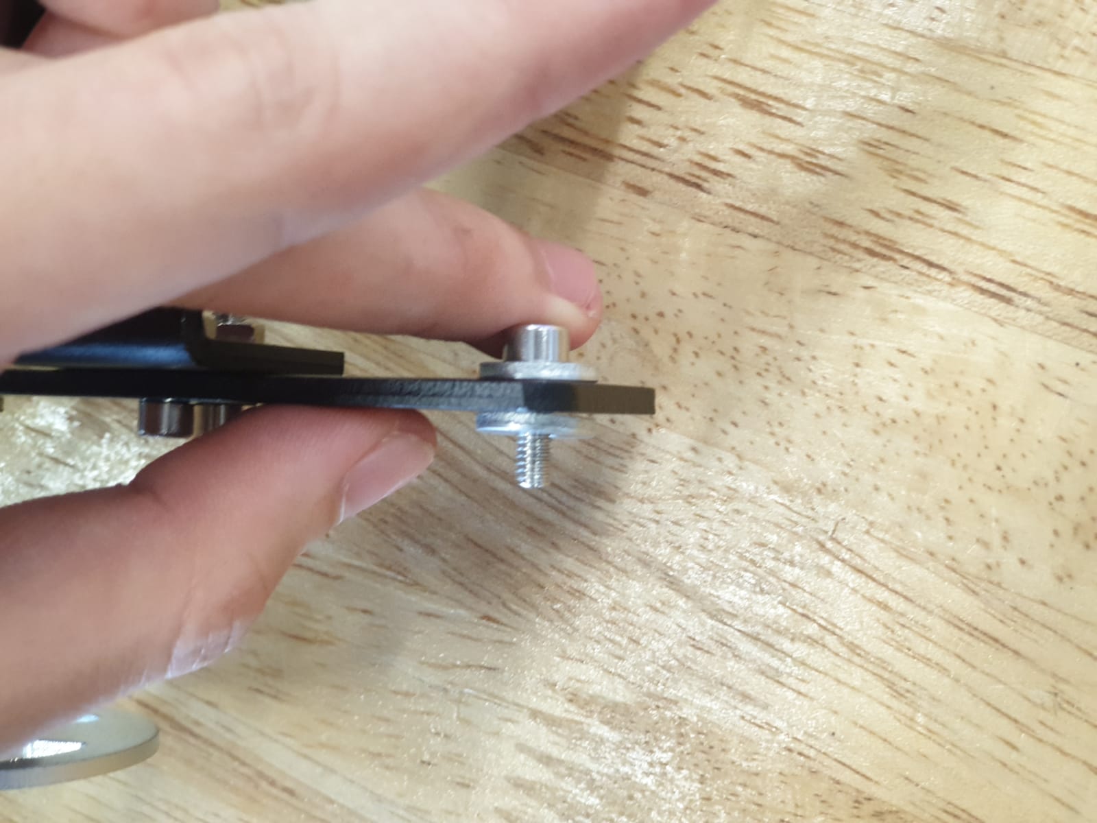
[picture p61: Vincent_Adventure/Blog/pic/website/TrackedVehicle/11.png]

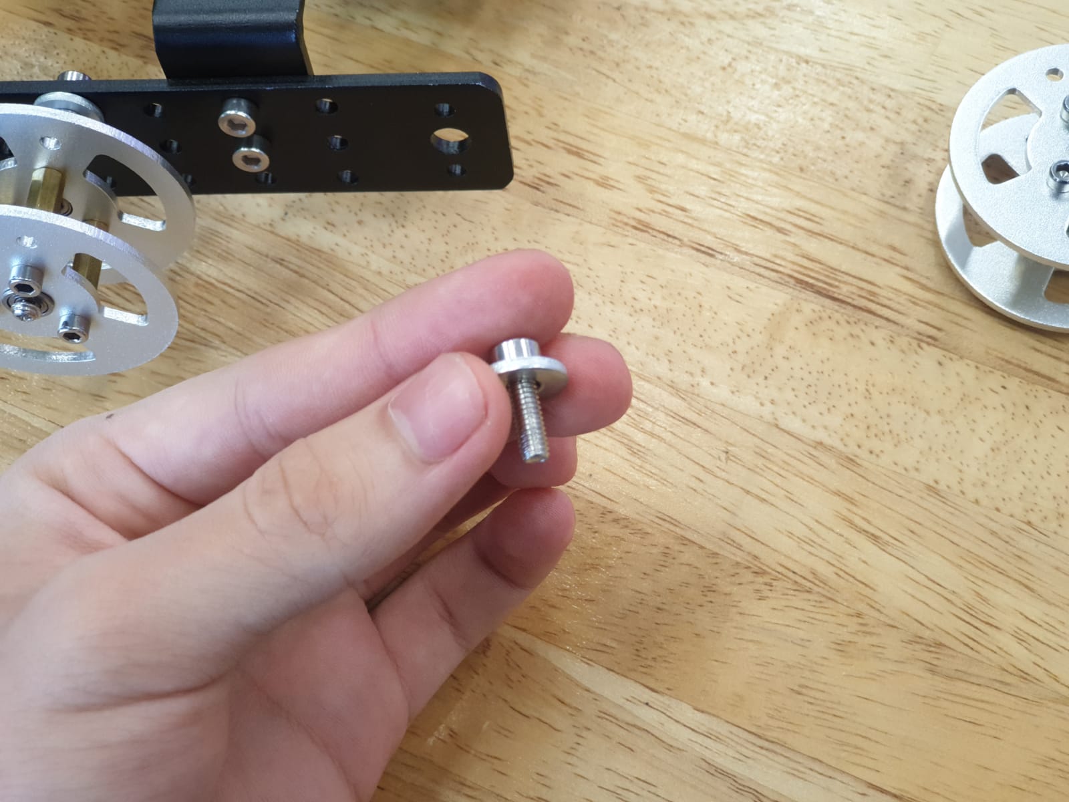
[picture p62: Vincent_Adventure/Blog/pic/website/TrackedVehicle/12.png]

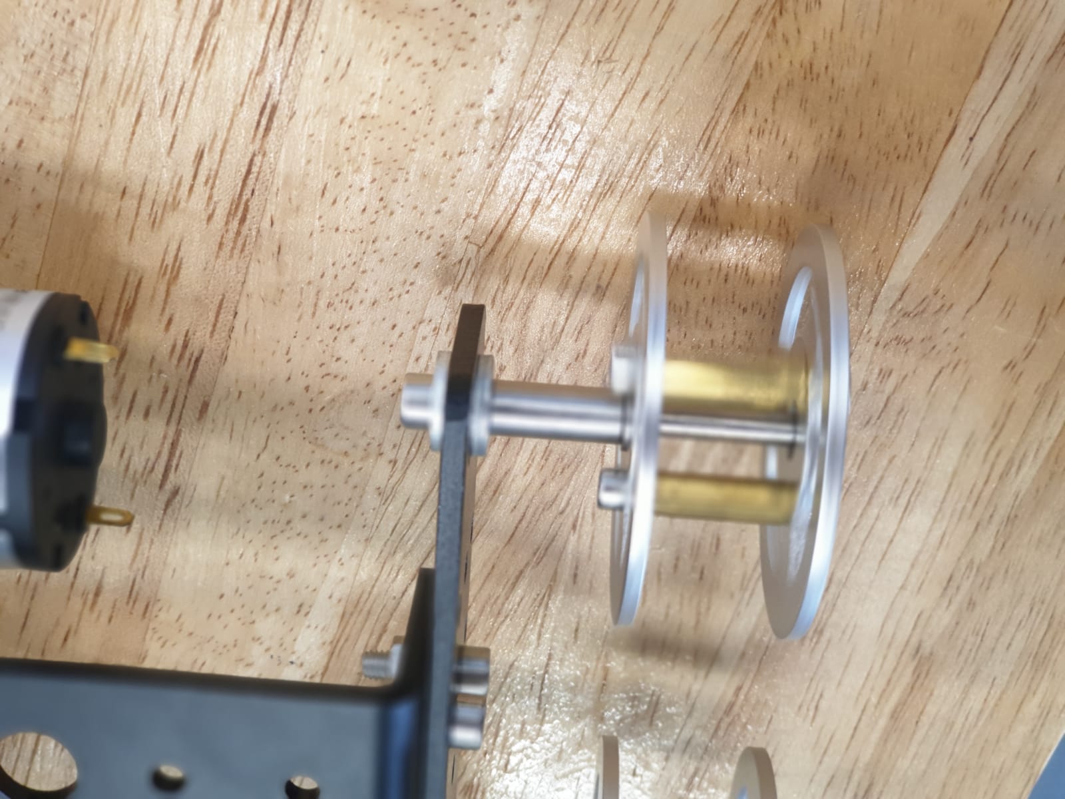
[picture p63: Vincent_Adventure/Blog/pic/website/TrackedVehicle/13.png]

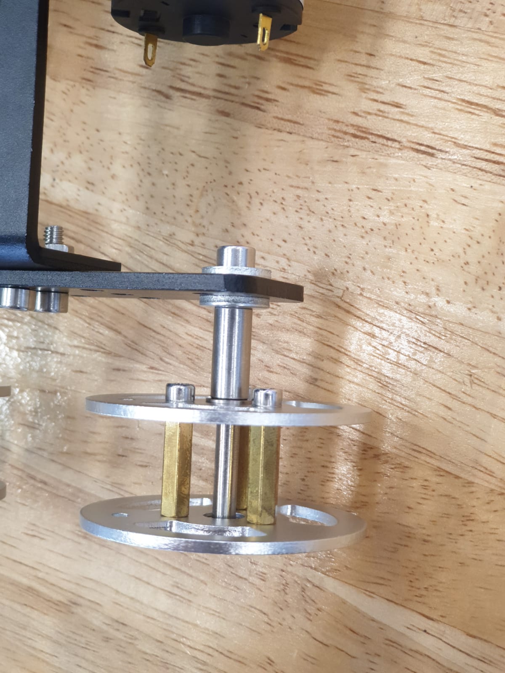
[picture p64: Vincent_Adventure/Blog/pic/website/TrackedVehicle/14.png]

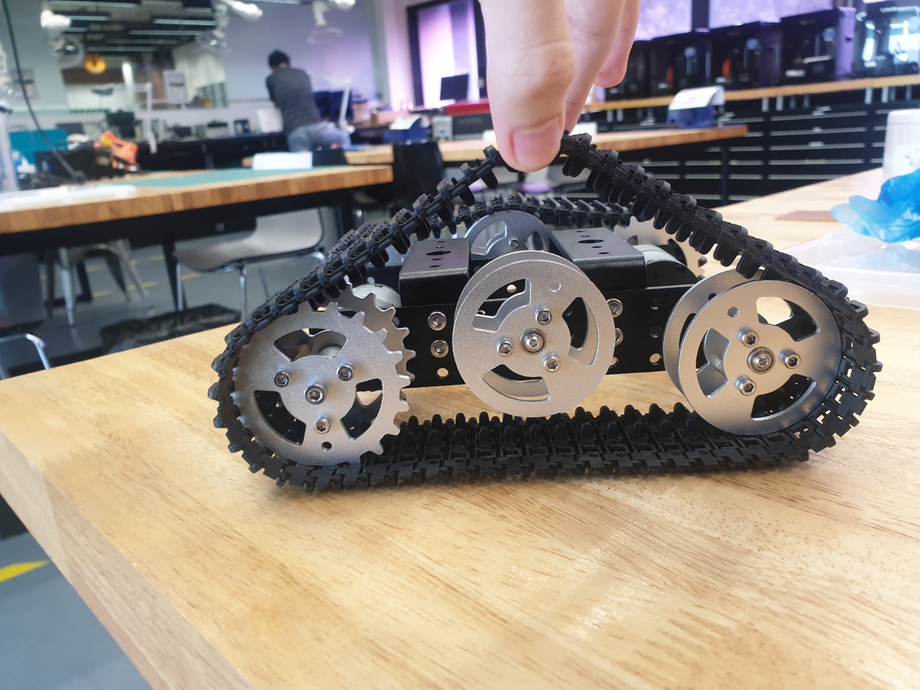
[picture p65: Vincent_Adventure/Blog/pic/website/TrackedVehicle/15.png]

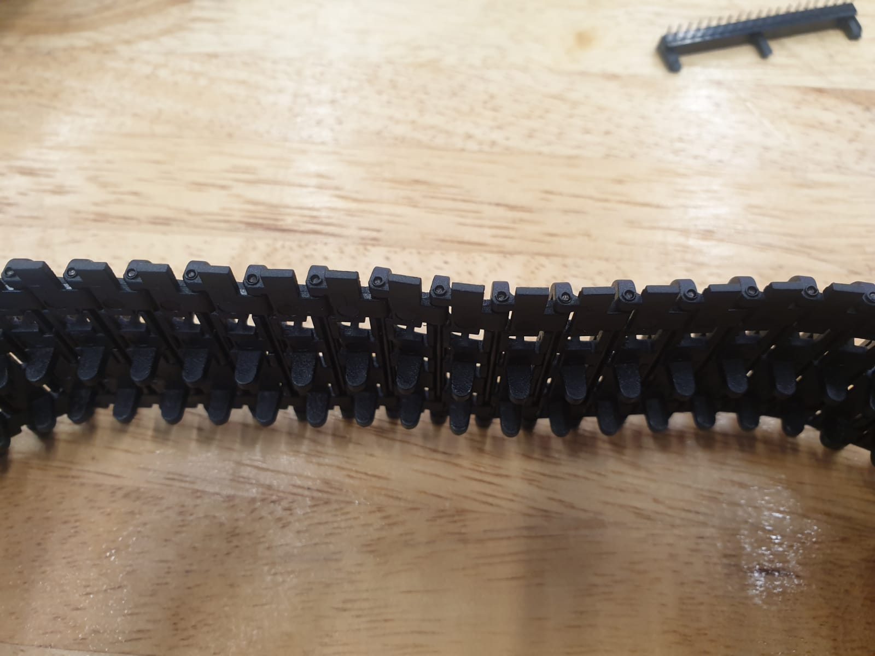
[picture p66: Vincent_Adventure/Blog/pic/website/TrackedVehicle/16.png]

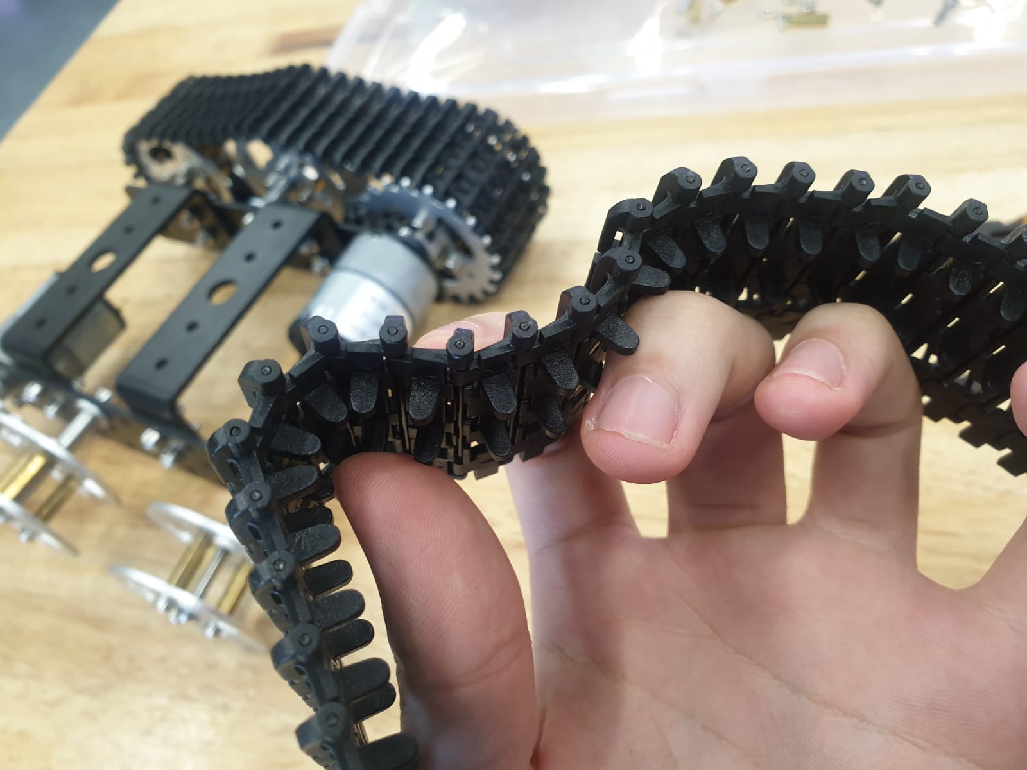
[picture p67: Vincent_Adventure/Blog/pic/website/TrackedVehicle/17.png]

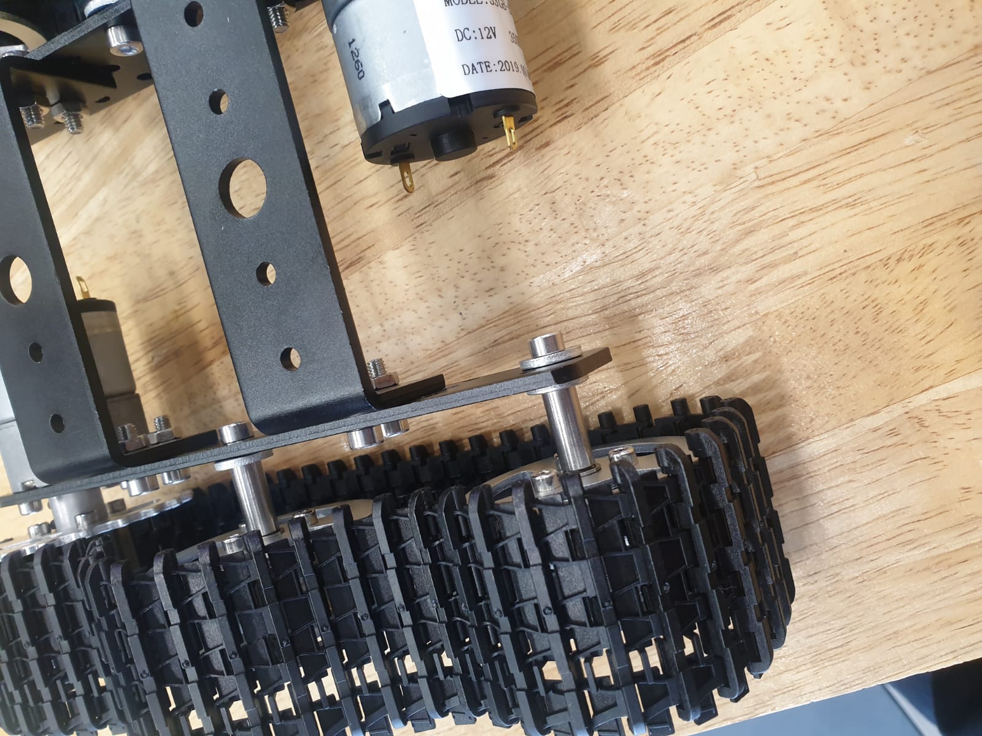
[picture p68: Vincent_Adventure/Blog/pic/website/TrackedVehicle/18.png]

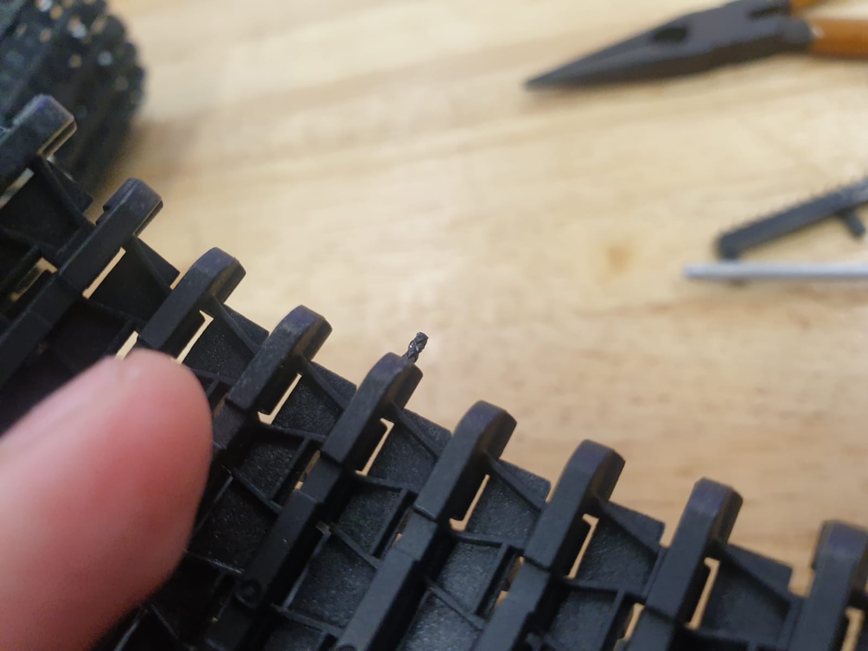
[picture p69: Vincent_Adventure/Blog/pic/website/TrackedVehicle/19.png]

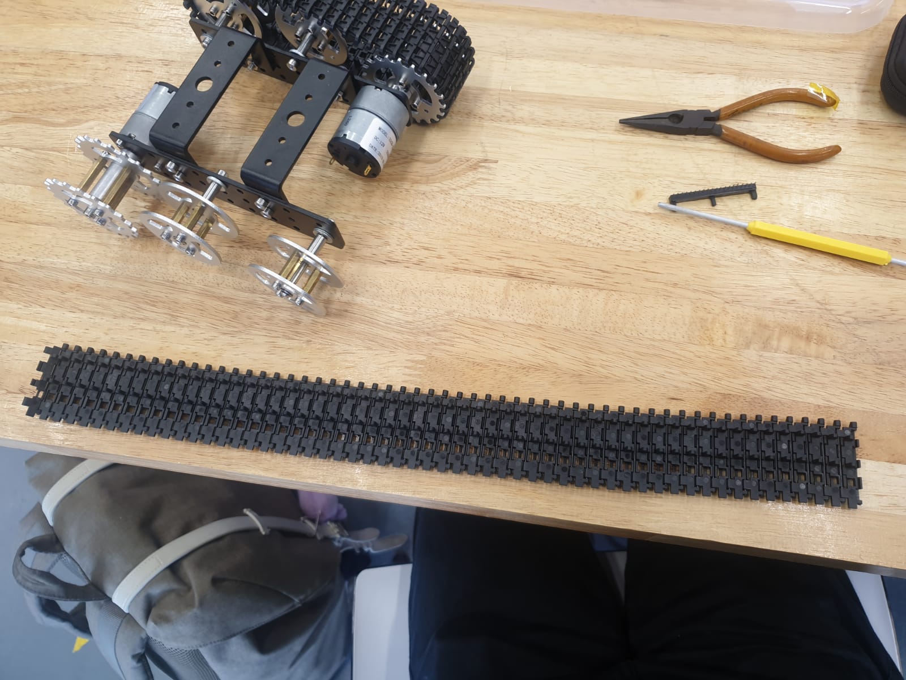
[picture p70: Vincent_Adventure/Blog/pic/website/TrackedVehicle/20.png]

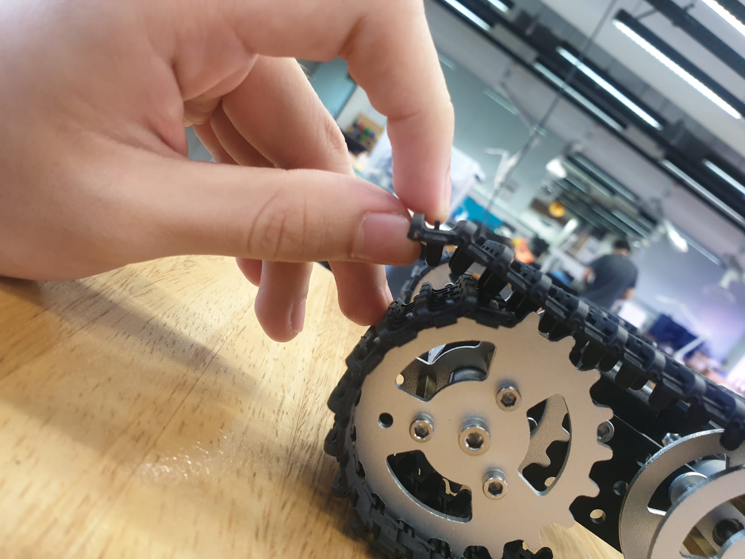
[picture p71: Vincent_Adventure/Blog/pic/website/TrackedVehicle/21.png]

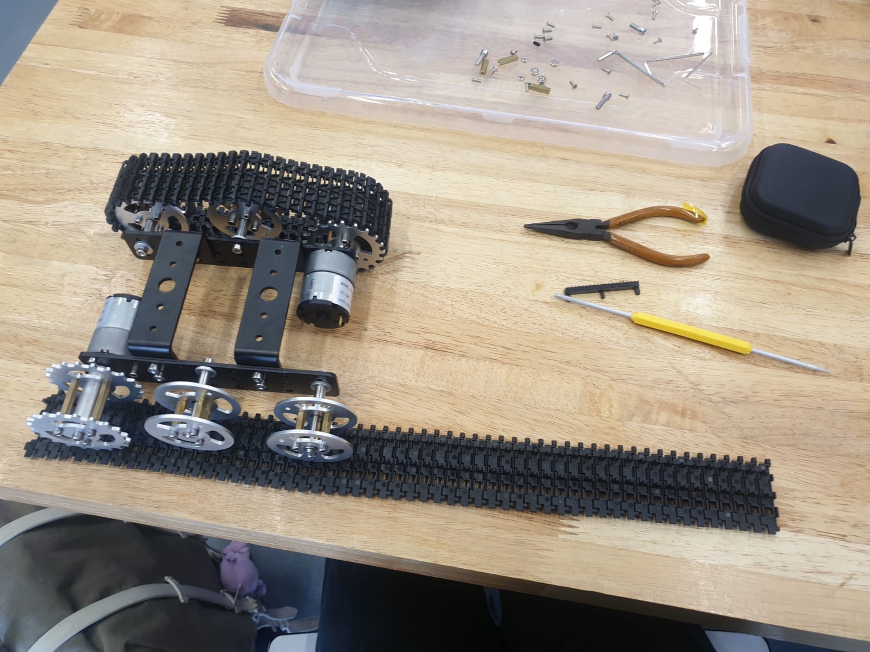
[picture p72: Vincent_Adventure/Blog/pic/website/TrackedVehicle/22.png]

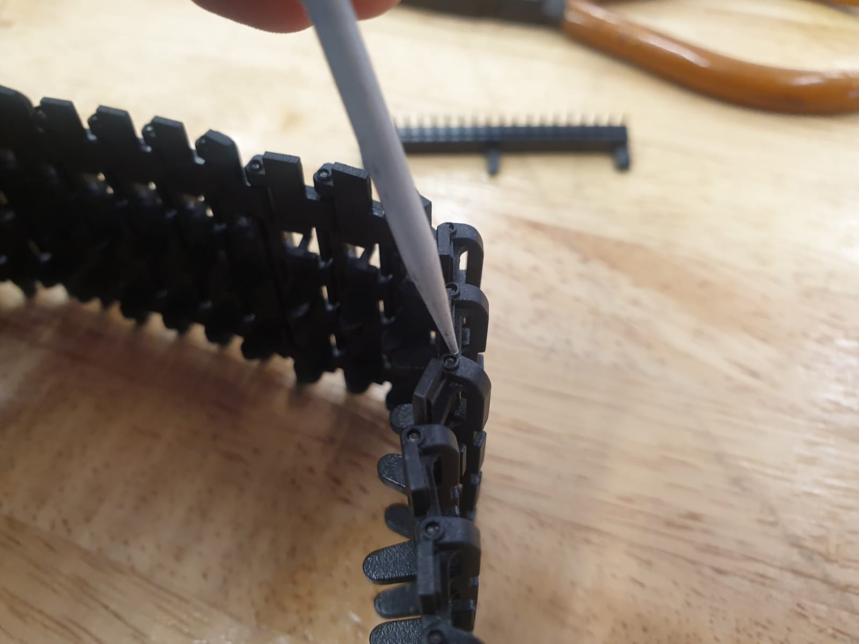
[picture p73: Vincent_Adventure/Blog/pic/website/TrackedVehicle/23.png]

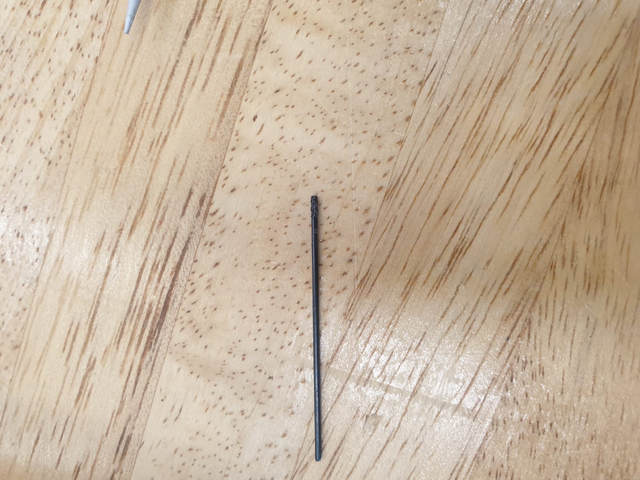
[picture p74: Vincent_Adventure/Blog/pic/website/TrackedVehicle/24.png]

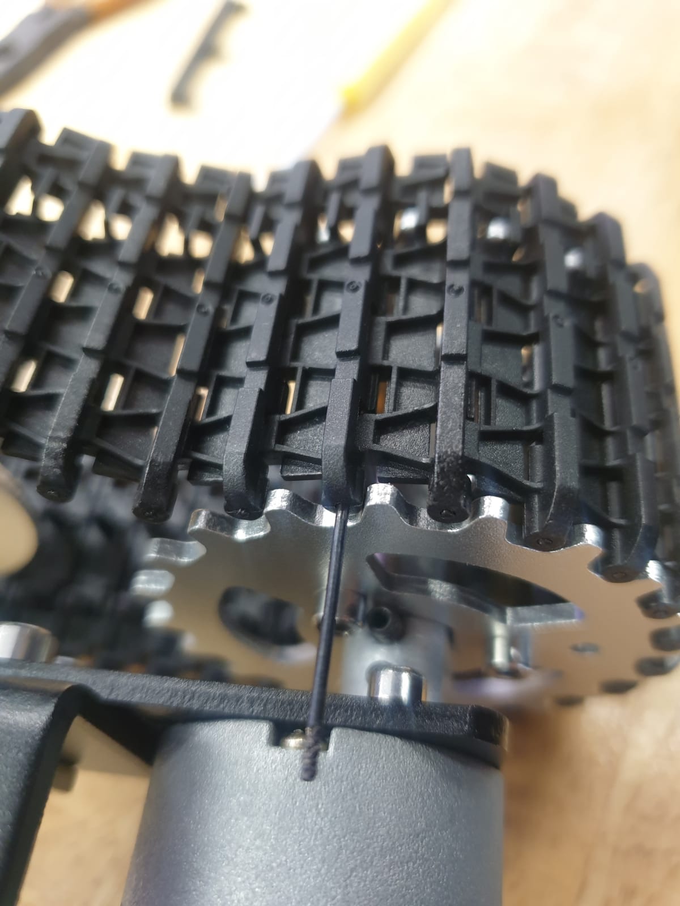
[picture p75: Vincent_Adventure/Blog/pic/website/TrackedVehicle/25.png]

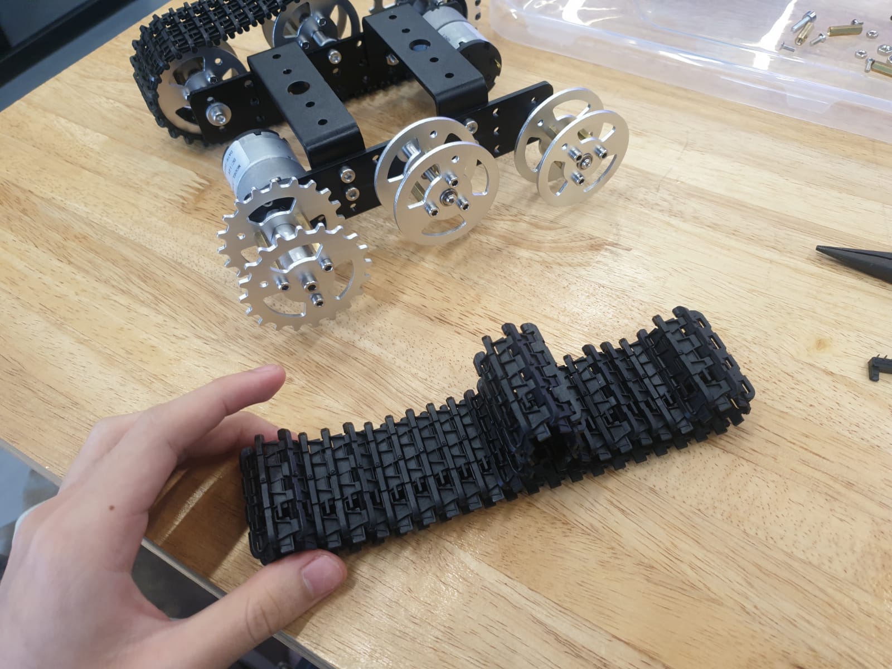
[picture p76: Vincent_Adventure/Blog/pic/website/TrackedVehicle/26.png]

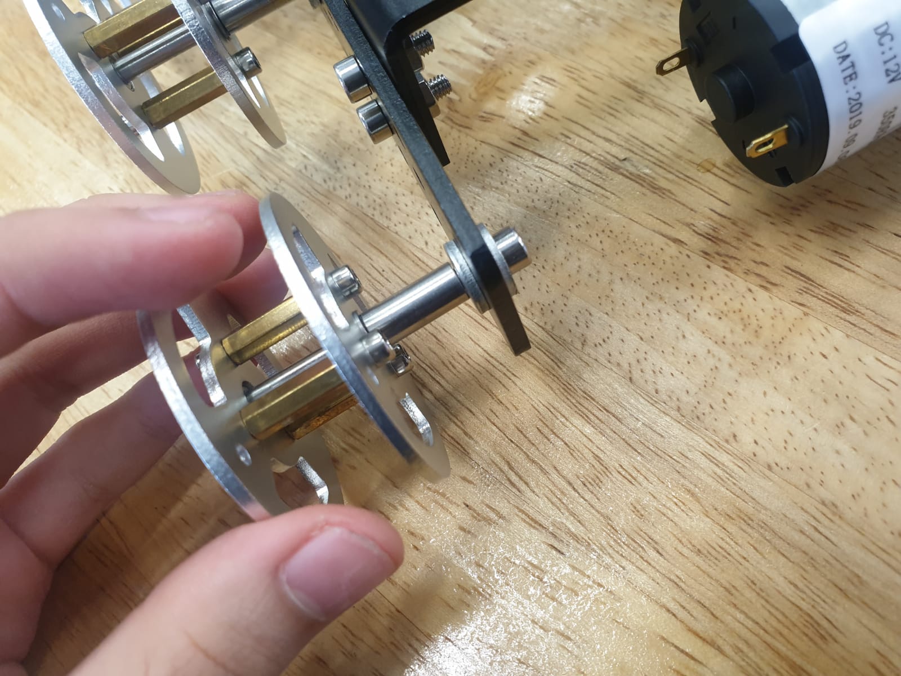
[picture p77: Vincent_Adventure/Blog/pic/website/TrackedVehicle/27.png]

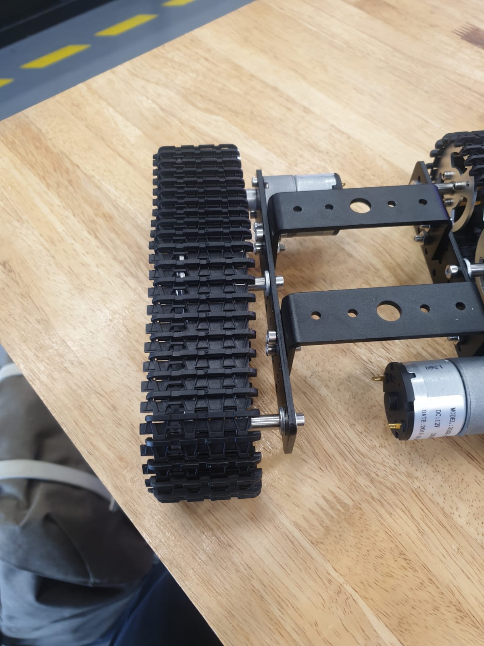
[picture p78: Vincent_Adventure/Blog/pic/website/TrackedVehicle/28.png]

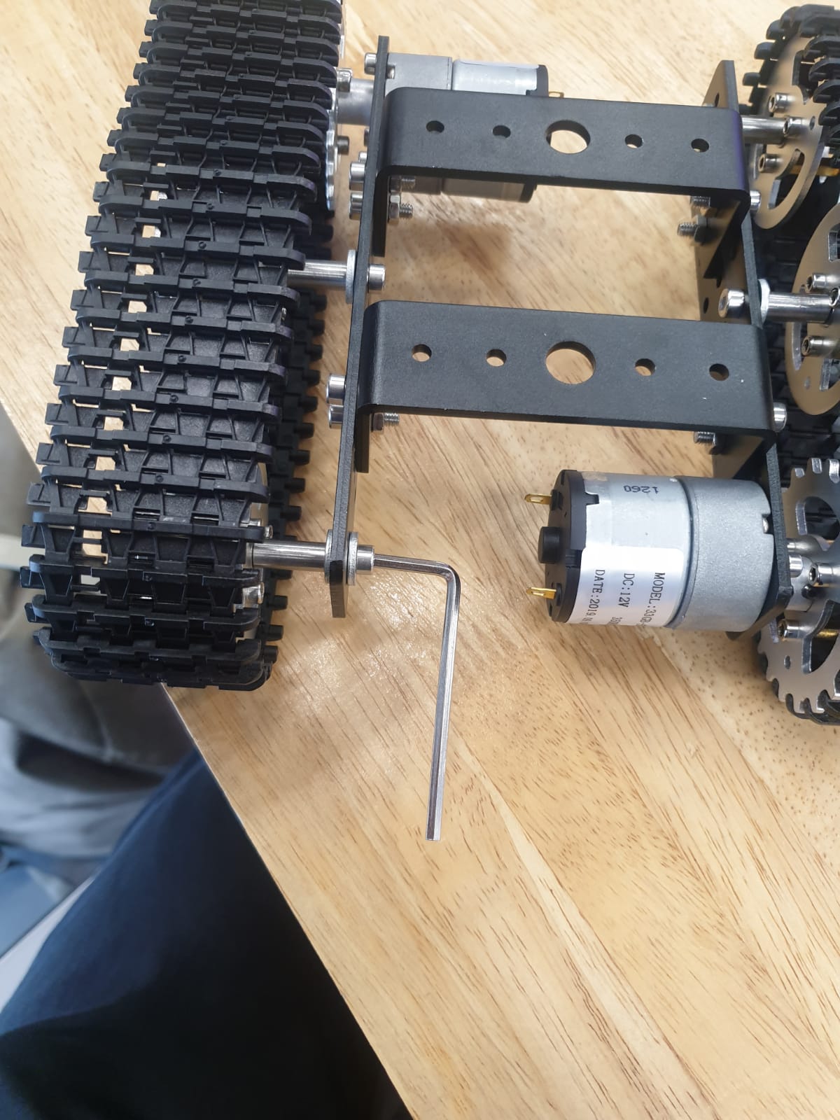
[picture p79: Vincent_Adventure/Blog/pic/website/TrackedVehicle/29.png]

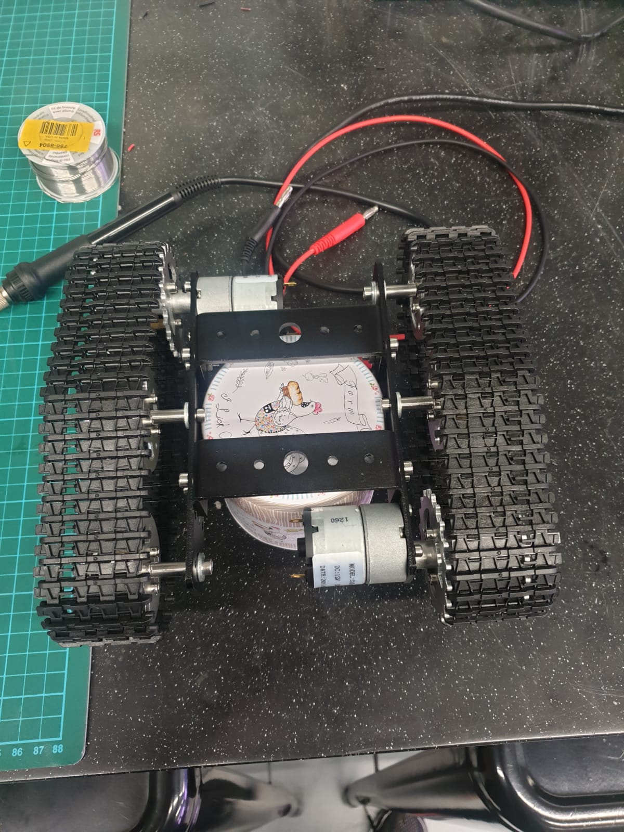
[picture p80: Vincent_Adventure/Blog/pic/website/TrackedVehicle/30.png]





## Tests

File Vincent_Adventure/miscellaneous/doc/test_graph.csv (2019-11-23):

time to reach max speed | Wheel motor torque
0.1 | 5.8736
0.2 | 3.5308
0.3 | 2.7499
0.4 | 2.3595
0.5 | 2.1252
0.6 | 1.969
0.7 | 1.8575
0.8 | 1.7738
0.9 | 1.7087
1 | 1.6567
1.1 | 1.6141
1.2 | 1.5786
1.3 | 1.5485
1.4 | 1.5228
1.5 | 1.5005
1.6 | 1.481
1.7 | 1.4637
1.8 | 1.4484
1.9 | 1.4347
2 | 1.4224
2.1 | 1.4112
2.2 | 1.4011
2.3 | 1.3918
2.4 | 1.3833
2.5 | 1.3755
2.6 | 1.3683
2.7 | 1.3616
2.8 | 1.3554
2.9 | 1.3497
3 | 1.3443

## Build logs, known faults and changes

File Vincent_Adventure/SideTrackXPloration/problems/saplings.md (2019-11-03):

# Saplings

### List of sites
* [Team Trees](https://teamtrees.org/)
* [Onetreeplanted](https://onetreeplanted.org/)

## Background
Recently, as of November 2019, there has been a movement towards rebuilding the forest. There has been a lot of sites where people around the world can donate their money to help support the organization to plant trees. When I was watching video on [Youtube](https://www.youtube.com/), I came across a shoutout from [Vat19](https://www.youtube.com/channel/UCDRbNGFusqlXX4a5vwi9ouQ) sharing about [Team Trees](https://teamtrees.org/). They stated that team trees will plant 1 tree for every $1 donated to their website. So I search for more similar movements on the internet and that is when I realized that there has been a lot of similar movements around the world.

## Problems
There are 2 main ways to grow trees. 1st is to plant the seeds. 2nd is to plant the saplings. There existing technological ways to plant seeds in the forest, which is by using a drone to disperse the seeds while flying. However, as of planting Saplings, I fail to find any robot to do this tiring task, especially when one is going to mass planting tree saplings. Even when we are in an era where technology is everywhere, saplings are still planted using manual labor.

### Benefits of Planting Saplings Instead of Seeds
By planting saplings, it will give a significant head start since the mature rate is shorter, which will result in a quicker visual impact. Therefore losing plants is lower to that as saplings.

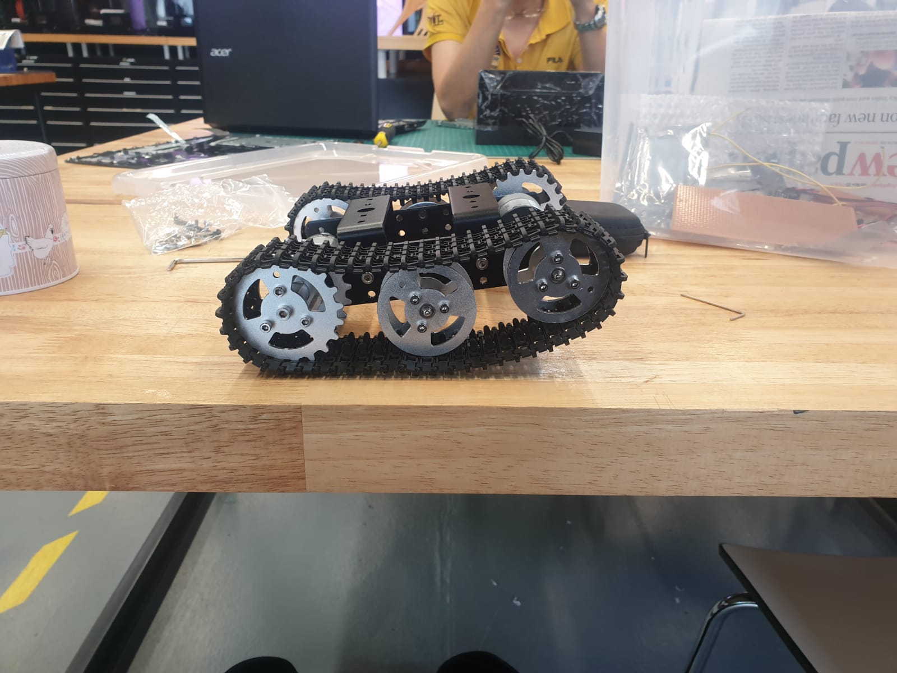
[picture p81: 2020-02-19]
Vincent_Adventure/Blog/pic/website/TrackedVehicle/FinalFailure.jpeg

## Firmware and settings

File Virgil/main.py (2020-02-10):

# Complete project details at https://RandomNerdTutorials.com

from machine import Pin, I2C
import ssd1306
from time import sleep

# ESP32 Pin assignment 
i2c = I2C(-1, scl=Pin(22), sda=Pin(21))

oled_width = 128
oled_height = 64
oled = ssd1306.SSD1306_I2C(oled_width, oled_height, i2c)

oled.text('In motion: False', 0, 0)
oled.text('Direction: Null', 0, 10)
oled.text('Planting: True', 0, 20)
        
oled.show()

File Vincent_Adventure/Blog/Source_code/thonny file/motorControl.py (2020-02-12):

from machine import Pin
import time
import machine
# =====================================================================
int1 = 4 #Brown
int2 = 0 #Red
int3 = 2  #Orange
int4 = 15  #Yellow
en1 = 17
en2 = 16
# =====================================================================
motor1a = Pin(int1,Pin.OUT)
motor1b = Pin(int2,Pin.OUT)
motor2a = Pin(int3,Pin.OUT)
motor2b = Pin(int4,Pin.OUT)
enLeft = machine.PWM(machine.Pin(en1),freq = 500,duty = 500)
enRight = machine.PWM(machine.Pin(en2),freq = 500,duty = 500)
# =====================================================================
def fwd():     
    motor1a(1)
    motor1b(0)
    motor2a(1)
    motor2b(0)
def stop():    #
    motor1a(0)
    motor1b(0)
    motor2a(0)
    motor2b(0)
def back():
    motor1a(0)
    motor1b(1)
    motor2a(0)
    motor2b(1)  
def rotationLeft():
    motor1a(1)
    motor1b(0)
    motor2a(0)
    motor2b(1)
def rotationRight():
    motor1a(0)
    motor1b(1)
    motor2a(1)
    motor2b(0)
def rest():
    stop()
    time.sleep(1)
# =====================================================================

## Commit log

2019-11-08 Create esp32 flashing
2019-11-08 Rename Flashing of esp32.md to Jeren/Flashing of esp32.md
2019-11-16 Update Flashing of esp32.md
2020-01-29 Sample code to test OLED
2020-02-04 Uploaded Schematic
2020-02-16 update workable code and design
    [beanstack.stl, border.dxf, espStore.stl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]
2020-02-18 Rename ModelTrackVehicleAssembly.md to MODEL TRACK VEHICLE ASSEMBLY.md
2020-02-18 Rename Flashing of esp32.md to FLASHING OF ESP32.md
2020-02-18 Create Charging Circuit.png
2020-02-18 Create Boost Circuit.png
2020-02-18 Create Boost Circuit with ESP32.png
2020-02-18 Create Battery Voltage.png
2020-02-19 update 1/20
    [TUBE2.stl, body2.stl]
2020-02-23 11/20 update
    [living hinge+body assembly.dxf, middle seperation.dxf, side of the vehicle.dxf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]
